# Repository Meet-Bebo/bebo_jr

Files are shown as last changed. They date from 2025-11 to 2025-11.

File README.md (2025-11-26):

# Bebo Jr: A small desktop half-humanoid

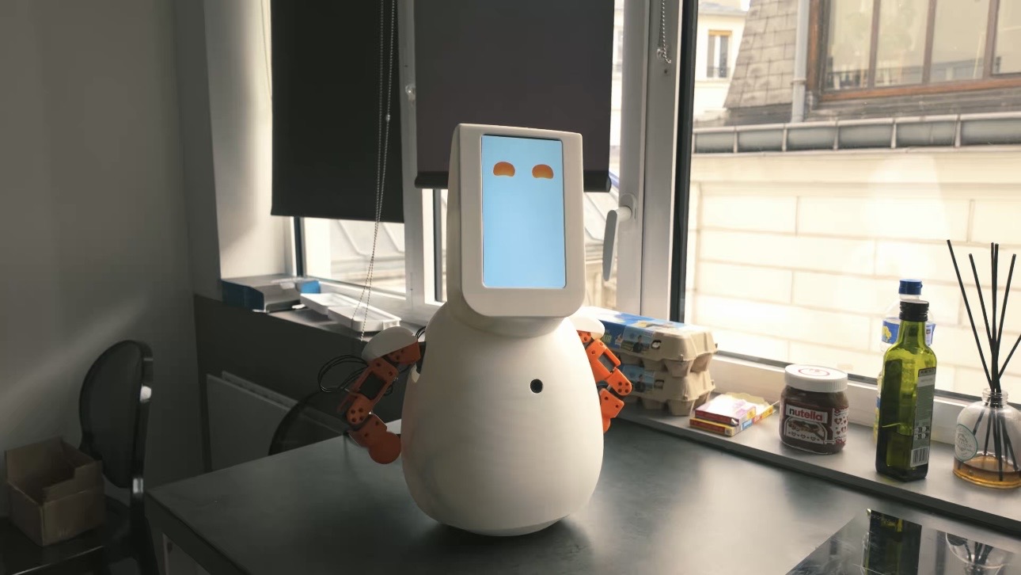
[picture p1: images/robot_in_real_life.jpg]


I built Bebo Jr as a small, affordable half-humanoid to tinker with human–robot interaction and motion re-targeting. It's inspired by Jibo, Moxie, Reachy Mini and other similiar desktop robots.

This repository holds all the files necessary to build Bebo Jr, including print and simulation files. The repository which contains Bebo Jr's runtime will be released later, since I'm actively working on it to adapt to other robotics form factor.

In this repository, I also provided simple scripts for motion retargeting using Inverse Kinematics for Bebo Jr as reference code for other people when working with the simulation files of Bebo Jr.

## How to build Bebo Jr

### Bill of Materials

| Item | Qty | Link | Est. price |
| --- | --- | --- | --- |
| ~5 |
| Raspberry Pi 5 (4GB) | 1 | https://www.amazon.fr/-/en/Raspberry-4GB-Quad-Core-ARMA76-64-bit/dp/B0CK3L9WD3 | ~80 |
| Waveshare motor driver | 1 | https://www.amazon.fr/dp/B0CJ6TP3TP | ~30 |
| XL330-M288T servo | 10  | https://emanual.robotis.com/docs/en/dxl/x/xl330-m288/ | ~55 each |
| 7\" HDMI display | 1 | https://www.amazon.fr/dp/B0CLLHGX54 | ~45 |
| ReSpeaker 2-Mic HAT for Pi | 1 | — | ~18 |
| Innomaker 720p camera | 1 | https://www.amazon.fr/-/en/InnoMaker-720P-Camera-DFOV-120%C2%B0/dp/B0CLRJZG8D | ~25 |
| 3W mini speaker (JST-PH2.0) | 1 | https://www.amazon.fr/-/en/QUARKZMAN-JST-PH2-0-Interface-Electronic-Advertising/dp/B0DB1WM4QR | ~12 |
| 6704-2RS bearings (20x27x4 mm) | 2 | https://www.amazon.fr/-/en/sourcing-6704-2RS-Groove-Bearing-20mmx27mmx4mm/dp/B0834WBWGS | ~8 each |
| Thin micro-HDMI cable | 1 | https://www.amazon.fr/dp/B0F1NFHK91 | ~10 |
| M3 heat-set inserts | 8 | — |

There are miscellaneous parts, such as wires, but they should be included when you buy the core components.

### Print the parts

All the `.3mf` files live in `print/`; I slice each once for a full set. My PLA baseline:

- Layers: 0.2 mm (0.16 mm for the head/screen mask)
- Shell: 3 perimeters; 4–5 solid top/bottom layers
- Infill: 20–30% gyroid or grid
- Temps: 0.4 mm nozzle at ~200–210 °C; bed 60 °C
- Supports: build-plate only for head shell and shoulders (tree/organic if available)
- Adhesion: brim on tall or narrow parts (arm segments, rotating base)
- Material: PLA is easiest; PETG works if I slow down and cool overhangs

The OnShape model can be used to reference on how build Bebo JR:
https://cad.onshape.com/documents/6693e038d6f5b2ee88eb0e81/w/837c8362b0b0bbf41939d6fd/e/ded7f450cb5bd722a96b42b6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

### Zero Position and Motor ID

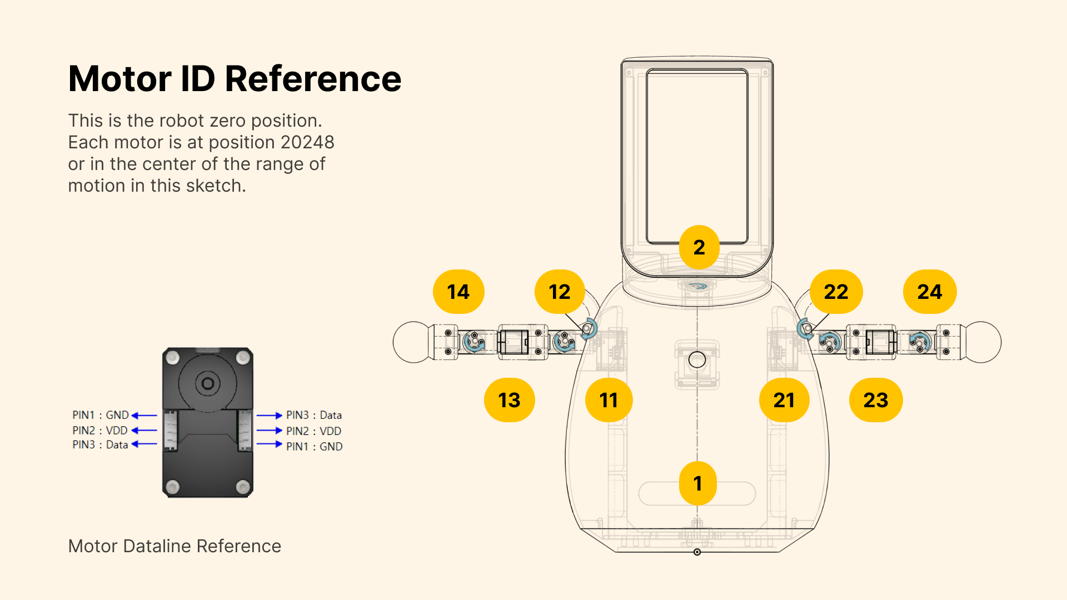
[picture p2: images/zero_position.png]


The zero position of Bebo Jr can be referenced from the above picture.

Prior to assembly, you should zero all motors and provide them with the ID shown above. Bebo Jr needs to be assembled so that in the above position, all motors should read zero, hence zero position. This reduces the amount of work necessary for calibration and sim-to-real when training policies on top of the robot.

## Simulation and Motion Retargeting

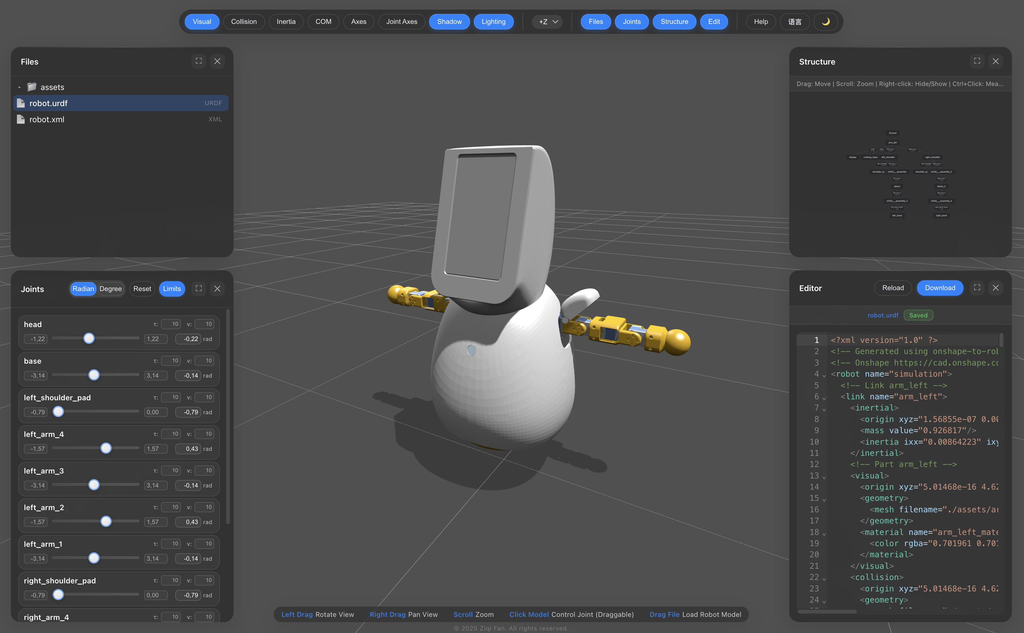
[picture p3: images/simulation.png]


You can test the IK teleop without assembling anything by running the simulation and motion re-targeting code.

The files for simulation in other software can be found in `simulation`. The format included are URDF and Mujoco.

### Setting up

The repository uses uv for dependency management. To run the re-targeting, run the following commands.

```bash
# Install uv if you haven't
curl -LsSf https://astral.sh/uv/install.sh | sh

# Sync dependencies
uv sync

# Run camera to robot teleop script.
uv run teleop/4_camera_robot_ik.py
```

You’ll need a camera for body tracking. It's still a bit buggy since monocular depth estimation isn't reliable on most body tracking software, especially mediapipe.

### Stages

You can learn more about each stages of the re-targeting pipeline below:

- `uv run teleop/1_body_tracking_camera.py` — capture pose from the camera and publish normalized landmarks.
- `uv run teleop/2_inverse_kinematics.py` — sinusoidal wrist targets driving the simulated arms.
- `uv run teleop/3_camera_robot_overlay.py` — camera feed with overlaid targets.
- `uv run teleop/4_camera_robot_ik.py` — full motion re-target: MediaPipe wrists driving both arms via IK.

## License

This project is GPL-3.0-or-later. You’re free to use, modify, and share it as long as derivatives stay under GPL-compatible terms.

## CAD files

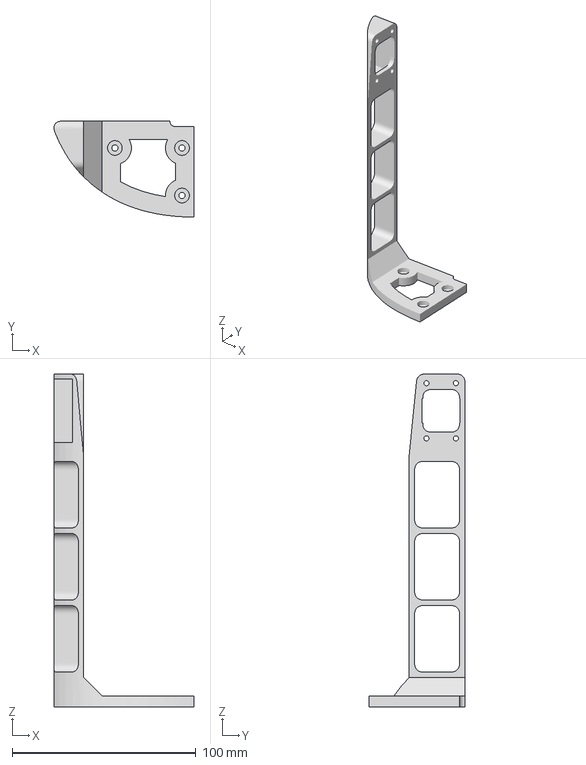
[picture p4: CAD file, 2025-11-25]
print/body/Main Body - Arm Left.3mf
76.1 x 52.3 x 181.0 mm

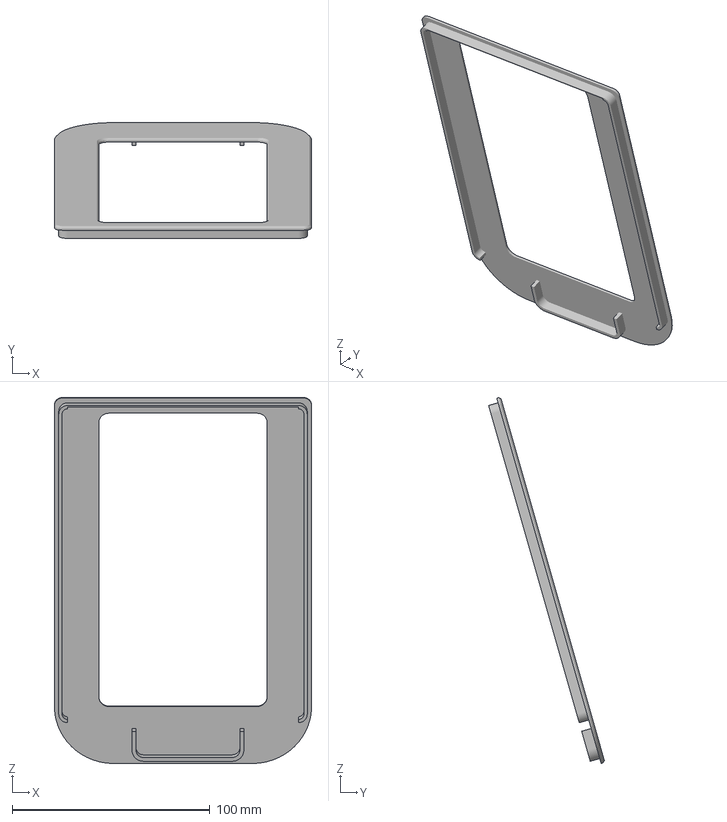
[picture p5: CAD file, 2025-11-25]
print/body/Main Body - Screen Mask.3mf
130.2 x 58.6 x 185.3 mm

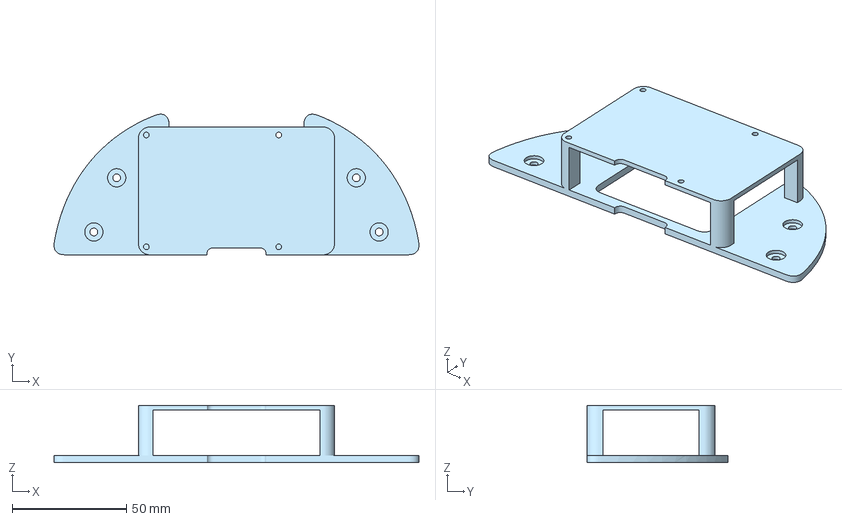
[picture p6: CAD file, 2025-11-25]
print/body/Main Body - Pi Mount.3mf
159.9 x 61.6 x 25.0 mm

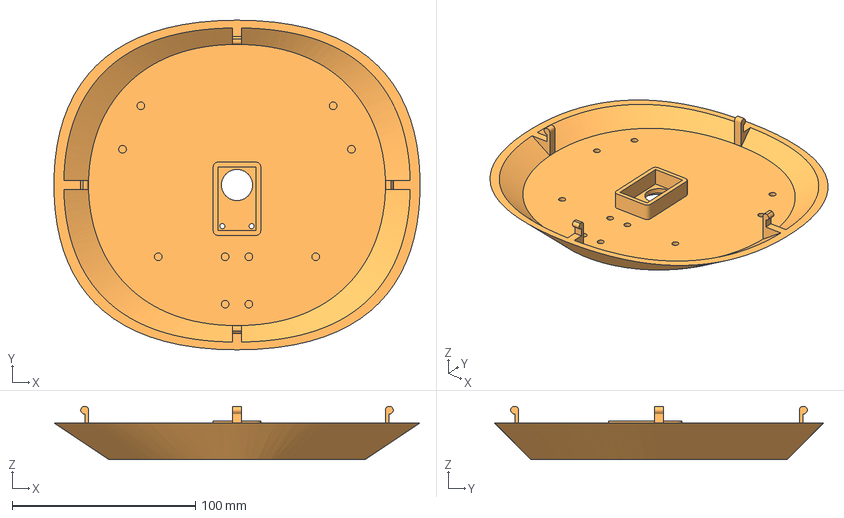
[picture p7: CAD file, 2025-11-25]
print/body/Main Body - Base.3mf
199.9 x 180.0 x 29.0 mm

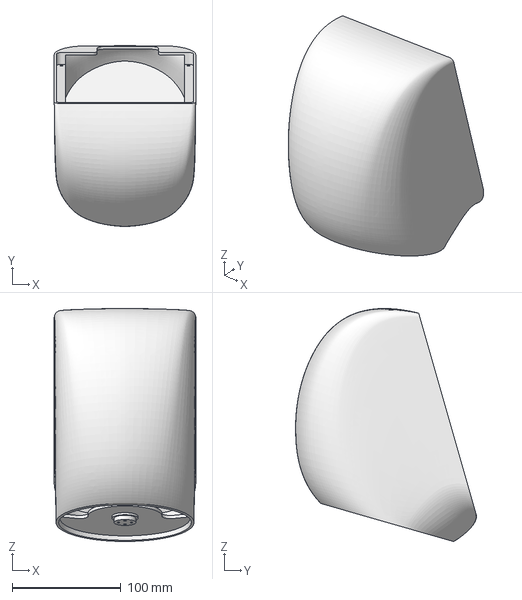
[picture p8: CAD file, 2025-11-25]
print/body/Main Body - Head.3mf
130.2 x 166.3 x 214.3 mm

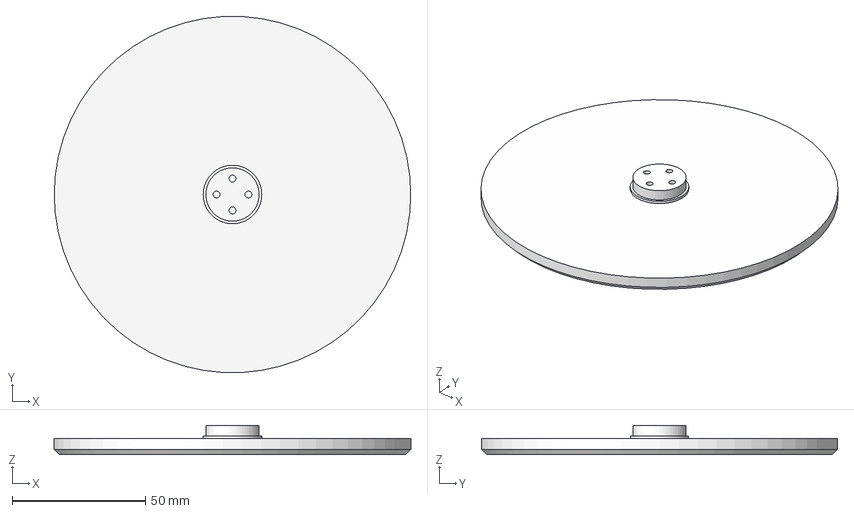
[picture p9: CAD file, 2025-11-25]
print/body/Main Body - Rotating Base.3mf
134.0 x 133.8 x 11.0 mm

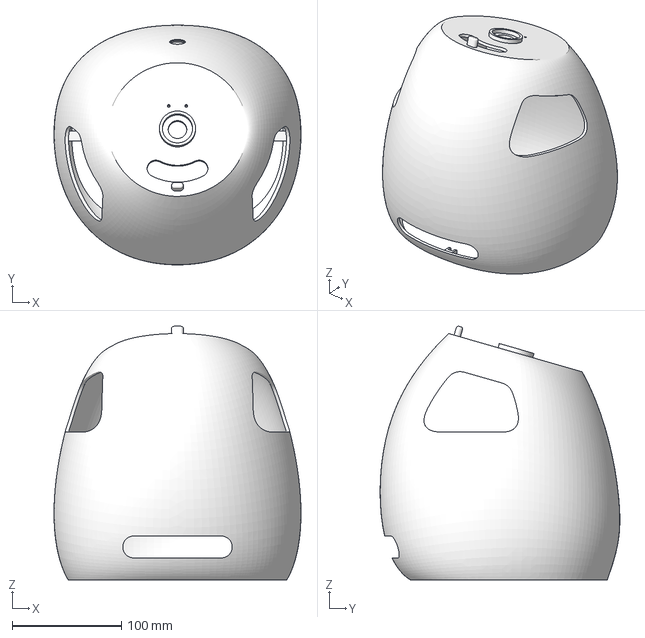
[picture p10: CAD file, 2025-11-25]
print/body/Main Body - Body.3mf
225.7 x 219.1 x 231.7 mm

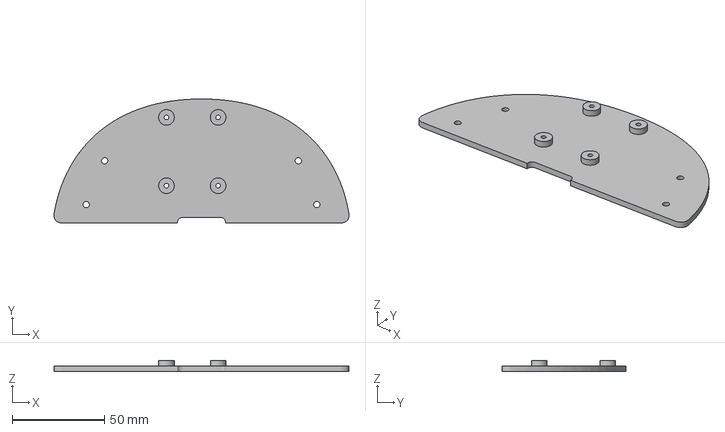
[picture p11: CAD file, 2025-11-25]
print/body/Main Body - Motor Driver Mount.3mf
159.9 x 67.3 x 6.00 mm

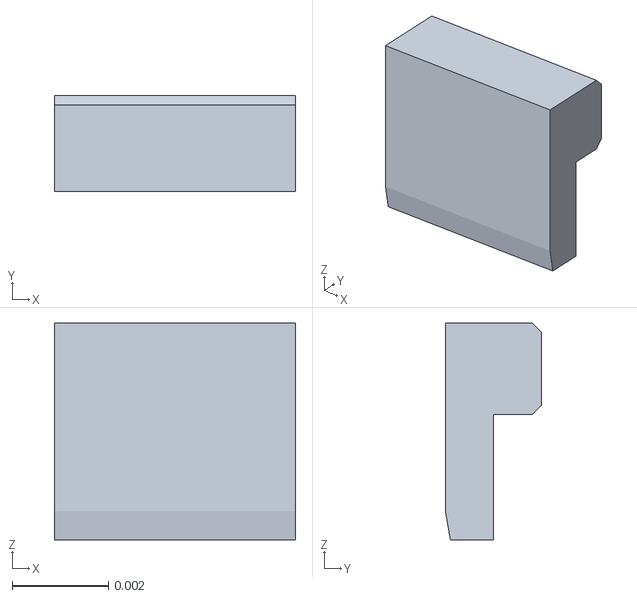
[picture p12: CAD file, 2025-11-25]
blender/phobos/bebo_jr/meshes/stl/dc15_a01_led_cap2_dummy.stl
0.005 x 0.002 x 0.0045

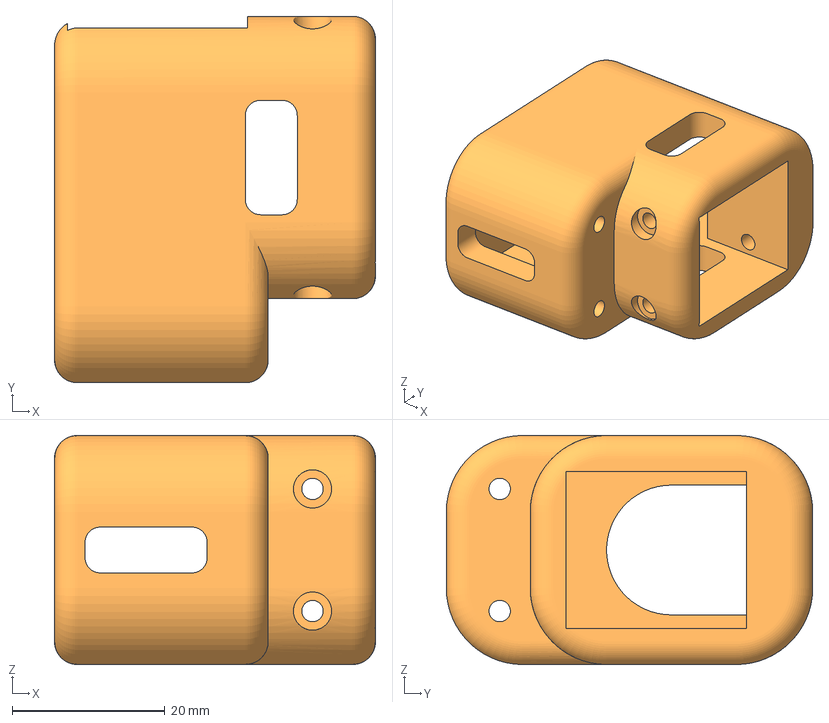
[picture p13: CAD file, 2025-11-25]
print/left_arm/Upperarm - Left Upperarm.3mf
42.1 x 48.0 x 30.0 mm

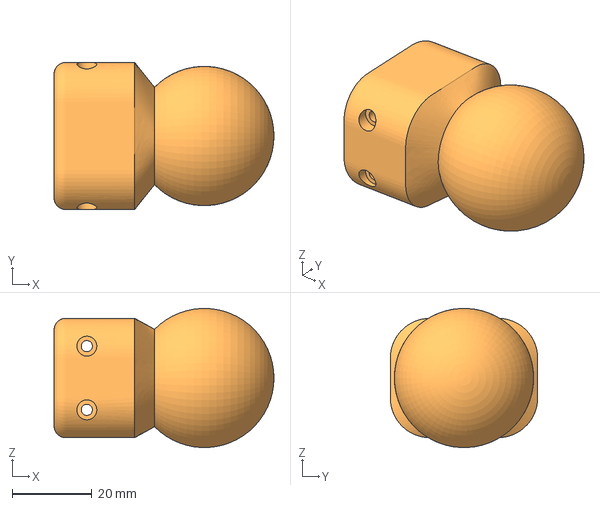
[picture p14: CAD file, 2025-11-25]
print/right_arm/Hand - Hand.3mf
55.3 x 37.0 x 34.9 mm

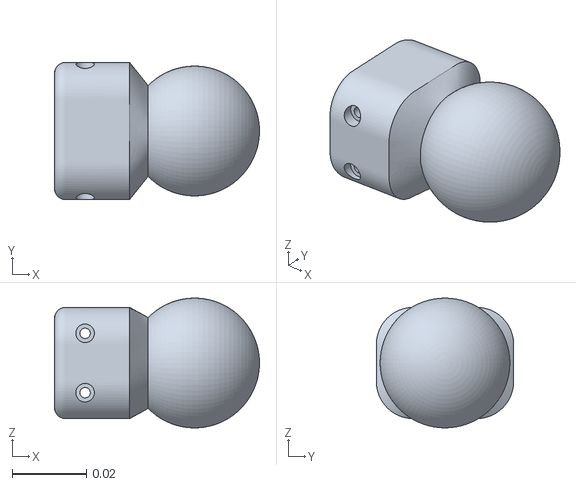
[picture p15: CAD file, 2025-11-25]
simulation/assets/hand.stl
0.0553 x 0.037 x 0.035

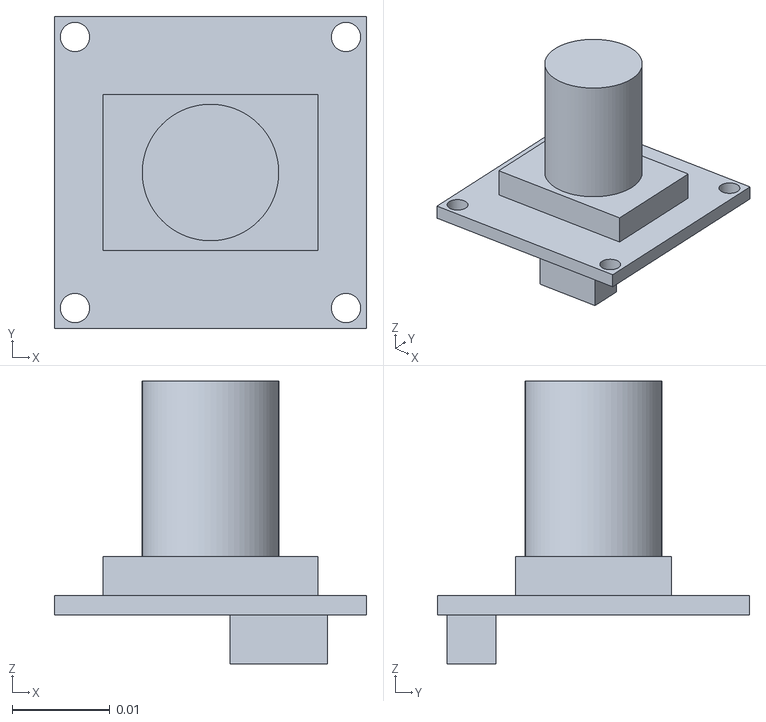
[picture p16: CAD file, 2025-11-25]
blender/phobos/bebo_jr/meshes/stl/camera.stl
0.032 x 0.032 x 0.029

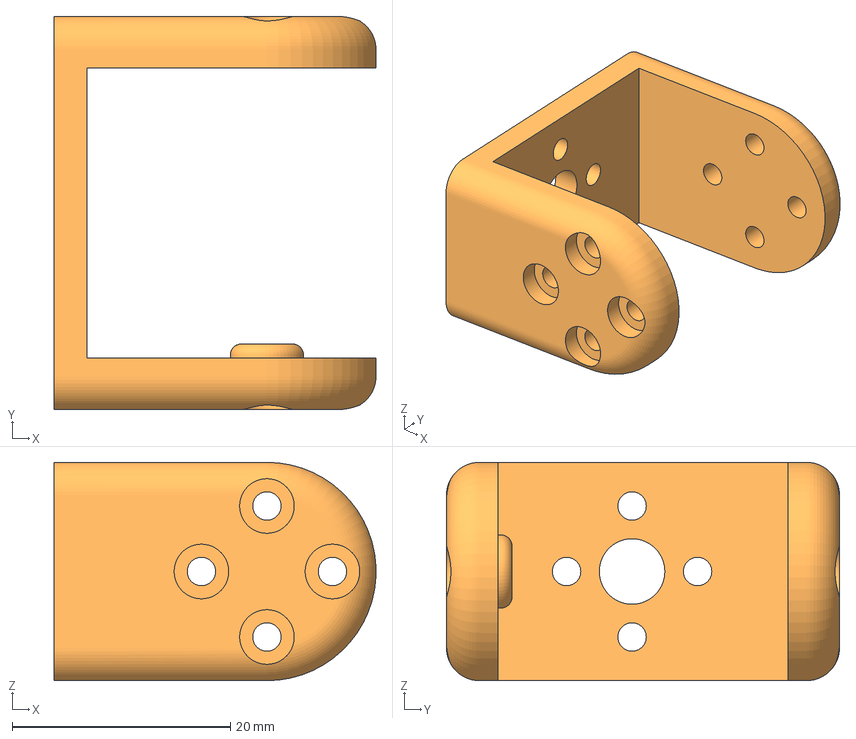
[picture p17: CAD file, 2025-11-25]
print/left_arm/Elbow - Elbow.3mf
29.5 x 36.0 x 20.0 mm

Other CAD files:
print/body/Main Body - Arm Right.3mf
print/right_arm/Upperarm - Right Upperarm.3mf
simulation/assets/pi_mount.stl
blender/phobos/bebo_jr/meshes/stl/left_upperarm.stl
blender/phobos/bebo_jr/meshes/stl/arm_left.stl
blender/phobos/bebo_jr/meshes/stl/arm_right.stl
blender/phobos/bebo_jr/meshes/stl/b3b_eh.stl
blender/phobos/bebo_jr/meshes/stl/base.stl
blender/phobos/bebo_jr/meshes/stl/body.stl
blender/phobos/bebo_jr/meshes/stl/bts2_m2_6x8.stl
blender/phobos/bebo_jr/meshes/stl/dc15_a01_case_b_dummy.stl
blender/phobos/bebo_jr/meshes/stl/dc15_a01_case_f_dummy.stl
blender/phobos/bebo_jr/meshes/stl/dc15_a01_case_m_dummy.stl
blender/phobos/bebo_jr/meshes/stl/dc15_a01_horn_dummy.stl
blender/phobos/bebo_jr/meshes/stl/display.stl
blender/phobos/bebo_jr/meshes/stl/elbow.stl
blender/phobos/bebo_jr/meshes/stl/head.stl
blender/phobos/bebo_jr/meshes/stl/left_shoulder.stl
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

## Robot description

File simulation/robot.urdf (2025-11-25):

<?xml version="1.0" ?>
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
<robot name="simulation">
  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
  <link name="arm_left">
    <inertial>
      <origin xyz="1.56855e-07 0.00536118 0.0913436" rpy="0 0 0"/>
      <mass value="0.926817"/>
      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
    </inertial>
    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
  </link>
  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
  <link name="display">
    <inertial>
      <origin xyz="-5.00413e-05 0.0320601 -0.0801642" rpy="0 0 0"/>
      <mass value="0.287621"/>
      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
    </inertial>
    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
  </link>
  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
  <joint name="head" type="revolute">
    <origin xyz="-1.15931e-17 -0.00602975 0.2275" rpy="2.86234 -7.59018e-16 -3.14159"/>
    <parent link="arm_left"/>
    <child link="display"/>
    <axis xyz="0 0 1"/>
    <limit effort="10" velocity="10" lower="-1.22173" upper="1.22173"/>
  </joint>
  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
  <link name="rotating_base">
    <inertial>
      <origin xyz="-1.64215e-19 -3.56062e-18 -0.00789183" rpy="0 0 0"/>
      <mass value="0.104547"/>
      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
    </inertial>
    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
  </link>
  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
  <joint name="base" type="revolute">
    <origin xyz="-1.44431e-34 6.12323e-19 0.008" rpy="-3.00927e-36 4.07832e-56 -3.14159"/>
    <parent link="arm_left"/>
    <child link="rotating_base"/>
    <axis xyz="0 0 1"/>
    <limit effort="10" velocity="10" lower="-3.14159" upper="3.14159"/>
  </joint>
  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
  <link name="left_shoulder">
    <inertial>
      <origin xyz="0.000954891 0.00228907 -0.0110516" rpy="0 0 0"/>
      <mass value="0.0105595"/>
      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
    </inertial>
    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
  </link>
  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
  <link name="shoulder_pad">
    <inertial>
      <origin xyz="0.0249562 0.0106205 -0.017979" rpy="0 0 0"/>
      <mass value="0.0123034"/>
      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
    </inertial>
    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
  </link>
  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
  <joint name="left_shoulder_pad" type="revolute">
    <origin xyz="0.0189997 0.0115 -0.0045" rpy="1.5708 0.785398 1.5708"/>
    <parent link="left_shoulder"/>
    <child link="shoulder_pad"/>
    <axis xyz="0 0 1"/>
    <limit effort="10" velocity="10" lower="-0.785398" upper="1.79856e-14"/>
  </joint>
  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
  <link name="xl330___assembly">
    <inertial>
      <origin xyz="-6.8305e-06 0.0295432 -0.0158499" rpy="0 0 0"/>
      <mass value="0.0655349"/>
      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
    </inertial>
    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
  </link>
  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
  <link name="elbow">
    <inertial>
      <origin xyz="-5.55112e-17 0.000935936 -0.0102895" rpy="0 0 0"/>
      <mass value="0.00742746"/>
      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
    </inertial>
    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
  </link>
  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
  <link name="xl330___assembly_2">
    <inertial>
      <origin xyz="-3.22999e-06 0.0310227 -0.0130404" rpy="0 0 0"/>
      <mass value="0.0702024"/>
      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
    </inertial>
    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
  </link>
  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
  <link name="left_hand">
    <origin xyz="0 0 0" rpy="0 -0 0"/>
    <inertial>
      <origin xyz="0 0 0" rpy="0 0 0"/>
      <mass value="1e-9"/>
      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
    </inertial>
  </link>
  <joint name="left_hand_frame" type="fixed">
    <origin xyz="-1.37945e-14 0.0695 -0.0136997" rpy="-1.5708 -1.5708 0"/>
    <parent link="xl330___assembly_2"/>
    <child link="left_hand"/>
    <axis xyz="0 0 0"/>
  </joint>
  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
  <joint name="left_arm_4" type="revolute">
    <origin xyz="-4.44089e-16 0.0142997 -0.0195" rpy="-1.5708 -4.19975e-14 4.43077e-14"/>
    <parent link="elbow"/>
    <child link="xl330___assembly_2"/>
    <axis xyz="0 0 1"/>
    <limit effort="10" velocity="10" lower="-1.5708" upper="1.5708"/>
  </joint>
  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
  <joint name="left_arm_3" type="revolute">
    <origin xyz="2.20102e-14 0.0576 -0.0122" rpy="1.5708 1.80868e-13 -4.21438e-13"/>
    <parent link="xl330___assembly"/>
    <child link="elbow"/>
    <axis xyz="0 0 1"/>
    <limit effort="10" velocity="10" lower="-3.14159" upper="3.14159"/>
  </joint>
  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
  <joint name="left_arm_2" type="revolute">
    <origin xyz="0.0142997 2.498e-16 -0.0245" rpy="-1.5708 -1.19571e-14 -1.5708"/>
    <parent link="left_shoulder"/>
    <child link="xl330___assembly"/>
    <axis xyz="0 0 1"/>
    <limit effort="10" velocity="10" lower="-1.5708" upper="1.5708"/>
  </joint>
  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
  <joint name="left_arm_1" type="revolute">
    <origin xyz="0.089 0.0375 0.179517" rpy="1.5708 4.6923e-15 -1.5708"/>
    <parent link="arm_left"/>
    <child link="left_shoulder"/>
    <axis xyz="0 0 1"/>
    <limit effort="10" velocity="10" lower="-3.14159" upper="3.14159"/>
  </joint>
  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
  <link name="right_shoulder">
    <inertial>
      <origin xyz="0.000954891 -0.00228907 -0.0110516" rpy="0 0 0"/>
      <mass value="0.0105595"/>
      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
    </inertial>
    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
  </link>
  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
  <link name="shoulder_pad_2">
    <inertial>
      <origin xyz="0.0249562 0.0106205 -0.017979" rpy="0 0 0"/>
      <mass value="0.0123034"/>
      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
    </inertial>
    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
  </link>
  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
  <joint name="right_shoulder_pad" type="revolute">
    <origin xyz="-0.017 -0.0115 -0.0045" rpy="1.5708 0.785398 -1.5708"/>
    <parent link="right_shoulder"/>
    <child link="shoulder_pad_2"/>
    <axis xyz="0 0 1"/>
    <limit effort="10" velocity="10" lower="-0.785398" upper="1.4766e-14"/>
  </joint>
  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
  <link name="xl330___assembly_3">
    <inertial>
      <origin xyz="-6.8549e-06 0.0295432 -0.0158499" rpy="0 0 0"/>
      <mass value="0.0655349"/>
      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
    </inertial>
    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
  </link>
  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
  <link name="elbow_2">
    <inertial>
      <origin xyz="0.000935936 -1.11022e-16 -0.0102895" rpy="0 0 0"/>
      <mass value="0.00742746"/>
      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
    </inertial>
    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
  </link>
  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
  <link name="xl330___assembly_4">
    <inertial>
      <origin xyz="-3.22983e-06 0.0310227 -0.0130404" rpy="0 0 0"/>
      <mass value="0.0702024"/>
      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
    </inertial>
    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
  </link>
  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
  <link name="right_hand">
    <origin xyz="0 0 0" rpy="0 -0 0"/>
    <inertial>
      <origin xyz="0 0 0" rpy="0 0 0"/>
      <mass value="1e-9"/>
      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
    </inertial>
  </link>
  <joint name="right_hand_frame" type="fixed">
    <origin xyz="1.65348e-10 0.0695 -0.0136997" rpy="-1.5708 -1.5708 0"/>
    <parent link="xl330___assembly_4"/>
    <child link="right_hand"/>
    <axis xyz="0 0 0"/>
  </joint>
  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
  <joint name="right_arm_4" type="revolute">
    <origin xyz="0.0142997 -2.77556e-16 -0.0195" rpy="-1.5708 1.96578e-13 -1.5708"/>
    <parent link="elbow_2"/>
    <child link="xl330___assembly_4"/>
    <axis xyz="0 0 1"/>
    <limit effort="10" velocity="10" lower="-1.5708" upper="1.5708"/>
  </joint>
  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
  <joint name="right_arm_3" type="revolute">
    <origin xyz="1.65325e-10 0.0576 -0.0122" rpy="1.5708 -1.5708 0"/>
    <parent link="xl330___assembly_3"/>
    <child link="elbow_2"/>
    <axis xyz="0 0 1"/>
    <limit effort="10" velocity="10" lower="-3.14159" upper="3.14159"/>
  </joint>
  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
  <joint name="right_arm_2" type="revolute">
    <origin xyz="0.0142997 -2.498e-16 -0.0245" rpy="-1.5708 -6.97562e-14 -1.5708"/>
    <parent link="right_shoulder"/>
    <child link="xl330___assembly_3"/>
    <axis xyz="0 0 1"/>
    <limit effort="10" velocity="10" lower="-1.5708" upper="1.5708"/>
  </joint>
  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
  <joint name="right_arm_1" type="revolute">
    <origin xyz="-0.089 0.0375 0.179517" rpy="-1.5708 4.28246e-14 -1.5708"/>
    <parent link="arm_left"/>
    <child link="right_shoulder"/>
    <axis xyz="0 0 1"/>
    <limit effort="10" velocity="10" lower="-3.14159" upper="3.14159"/>
  </joint>
</robot>

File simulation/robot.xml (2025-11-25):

<?xml version="1.0" ?>
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
<mujoco model="simulation">
  <compiler angle="radian" meshdir="assets" autolimits="true"/>
  <default>
    <default class="simulation">
      <joint frictionloss="0.1" armature="0.005"/>
      <position kp="50" dampratio="1"/>
      <default class="visual">
        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
      </default>
      <default class="collision">
        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
      </default>
    </default>
  </default>
  <worldbody>
    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
    <body name="arm_left" pos="0 0 0" quat="1 0 0 0" childclass="simulation">
      <freejoint name="arm_left_freejoint"/>
      <inertial pos="1.56855e-07 0.00536118 0.0913436" mass="0.926817" fullinertia="0.00864223 0.00898484 0.00689434 7.3434e-07 -7.3209e-08 -0.000208978"/>
      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
      <body name="display" pos="-1.15931e-17 -0.00602975 0.2275" quat="1.11022e-16 -1.90928e-16 -0.990268 -0.139173">
        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
        <joint axis="0 0 1" name="head" type="hinge" range="-1.2217304763960297 1.2217304763960315"/>
        <inertial pos="-5.00413e-05 0.0320601 -0.0801642" mass="0.287621" fullinertia="0.00184599 0.00175481 0.00143822 -2.13386e-06 1.99291e-06 0.000397539"/>
        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
      </body>
      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
      <body name="rotating_base" pos="-1.44431e-34 6.12323e-19 0.008" quat="1.35525e-20 0 0 -1">
        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
        <joint axis="0 0 1" name="base" type="hinge" range="-3.141592653589793 3.141592653589793"/>
        <inertial pos="-1.64215e-19 -3.56062e-18 -0.00789183" mass="0.104547" fullinertia="0.00011678 0.00011678 0.000232844 -3.67342e-40 -4.73347e-60 -3.49268e-40"/>
        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
      </body>
      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
      <body name="left_shoulder" pos="0.089 0.0375 0.179517" quat="0.5 0.5 -0.5 -0.5">
        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
        <joint axis="0 0 1" name="left_arm_1" type="hinge" range="-3.14159265358978 3.1415926535898064"/>
        <inertial pos="0.000954891 0.00228907 -0.0110516" mass="0.0105595" fullinertia="1.49349e-06 2.9353e-06 2.46233e-06 -1.08642e-09 -1.06526e-08 -1.55193e-07"/>
        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
        <body name="shoulder_pad" pos="0.0189997 0.0115 -0.0045" quat="0.653281 0.270598 0.653281 0.270598">
          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
          <joint axis="0 0 1" name="left_shoulder_pad" type="hinge" range="-0.7853981633974303 1.7985612998927536e-14"/>
          <inertial pos="0.0249562 0.0106205 -0.017979" mass="0.0123034" fullinertia="3.51415e-06 6.33798e-06 4.31141e-06 3.49578e-07 -3.32541e-09 1.93855e-09"/>
          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
        </body>
        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
        <body name="xl330___assembly" pos="0.0142997 2.498e-16 -0.0245" quat="0.5 -0.5 0.5 -0.5">
          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
          <joint axis="0 0 1" name="left_arm_2" type="hinge" range="-1.5707963267944276 1.5707963267953655"/>
          <inertial pos="-6.8305e-06 0.0295432 -0.0158499" mass="0.0655349" fullinertia="3.34493e-05 1.25704e-05 2.88274e-05 7.73712e-11 -1.54866e-09 4.35359e-06"/>
          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
          <body name="elbow" pos="2.20102e-14 0.0576 -0.0122" quat="0.707107 0.707107 -8.4599e-14 -2.13686e-13">
            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
            <joint axis="0 0 1" name="left_arm_3" type="hinge" range="-3.1415926535897487 3.1415926535898375"/>
            <inertial pos="-5.55112e-17 0.000935936 -0.0102895" mass="0.00742746" fullinertia="2.01225e-06 7.75241e-07 1.69897e-06 2.52375e-14 2.28522e-21 -7.71319e-09"/>
            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
            <body name="xl330___assembly_2" pos="-4.44089e-16 0.0142997 -0.0195" quat="0.707107 -0.707107 -2.9754e-14 2.42493e-15">
              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
              <joint axis="0 0 1" name="left_arm_4" type="hinge" range="-1.5707963267948557 1.5707963267949374"/>
              <inertial pos="-3.22999e-06 0.0310227 -0.0130404" mass="0.0702024" fullinertia="3.54653e-05 9.41966e-06 3.39167e-05 -3.77028e-09 -1.27954e-11 1.44438e-06"/>
              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
            </body>
          </body>
        </body>
      </body>
      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
      <body name="right_shoulder" pos="-0.089 0.0375 0.179517" quat="0.5 -0.5 0.5 -0.5">
        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
        <joint axis="0 0 1" name="right_arm_1" type="hinge" range="-3.14159265358974 3.1415926535898464"/>
        <inertial pos="0.000954891 -0.00228907 -0.0110516" mass="0.0105595" fullinertia="1.4935e-06 2.9353e-06 2.46233e-06 1.08652e-09 -1.06527e-08 1.55193e-07"/>
        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
        <body name="shoulder_pad_2" pos="-0.017 -0.0115 -0.0045" quat="0.270598 0.653281 -0.270598 -0.653281">
          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
          <joint axis="0 0 1" name="right_shoulder_pad" type="hinge" range="-0.7853981633974335 1.4765966227514582e-14"/>
          <inertial pos="0.0249562 0.0106205 -0.017979" mass="0.0123034" fullinertia="3.51415e-06 6.33798e-06 4.31141e-06 3.49578e-07 -3.32541e-09 1.93855e-09"/>
          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
        </body>
        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
        <body name="xl330___assembly_3" pos="0.0142997 -2.498e-16 -0.0245" quat="0.5 -0.5 0.5 -0.5">
          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
          <joint axis="0 0 1" name="right_arm_2" type="hinge" range="-1.5707963267948264 1.5707963267949667"/>
          <inertial pos="-6.8549e-06 0.0295432 -0.0158499" mass="0.0655349" fullinertia="3.34493e-05 1.25704e-05 2.88274e-05 7.41815e-11 -1.56344e-09 4.35359e-06"/>
          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
          <body name="elbow_2" pos="1.65325e-10 0.0576 -0.0122" quat="0.5 0.5 -0.5 0.5">
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
